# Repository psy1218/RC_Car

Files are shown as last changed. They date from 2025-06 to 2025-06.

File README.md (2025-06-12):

# 🚗 RC Car, R9DS, AT9을 이용한 수동/자동 주행 시스템 구현

> **팀 이름**: 배경근  
> **팀원**: 201901973 배경근, 202201658 박소윤  

---

## 📁 GitHub 디렉토리 구조

### 현재 레포 구조

### 폴더 설명

- **RCcar/**  
  → 최종 통합 버전. 수동/자동/긴급사출/LED 제어가 모두 포함됨.  
  → `cpp/`: 아두이노 제어 코드, `python/`: 라인트레이싱 영상처리 코드

- **auto_mode/**  
  → 자동 주행 실험용. ROI 영역 실험, 필터링 비교 등 테스트 중심

- **manual_mode/**  
  → 수동 조작 실험용. ESC 속도 감쇠 및 PWM LED 점등 테스트

---

### 과거 레포 구조

- **RCcar/**: 수동제어와 LED 제어 코드 
- **auto_detection/**: 영상 기반 라인 인식 초기 실험
- **control/**: 조향 및 속도 제어 실험, PlatformIO 기반

---

---

## 🔔 주의사항 

- 본 프로젝트는 처음에는 기존의 과제 레포에서 진행되었습니다.  
- 하지만 새로운 기능 및 문서화를 위해 별도의 새로운 레포를 생성하였고, 커밋 이력은 초기화되었습니다.  
- 기존 개발 히스토리와 구현 흐름이 궁금한 경우, [**기존 레포지토리 링크(클릭!!)**](https://github.com/psy1218/blink/tree/main/RC_car_project)를 참고해 주세요.

---

## 🎬 실행 영상 - 이미지를 클릭해보세요! 

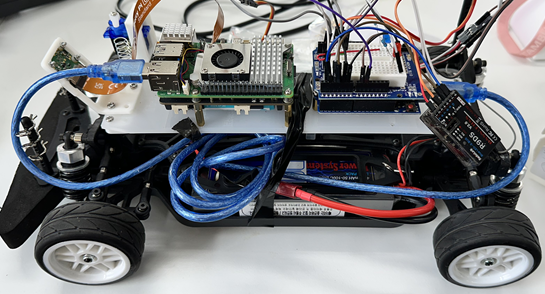
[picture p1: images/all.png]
프로젝트 시연 영상 (https://youtu.be/iogF90Vy1ic)


## 📷 RC카 관련 이미지 
<p align="center">
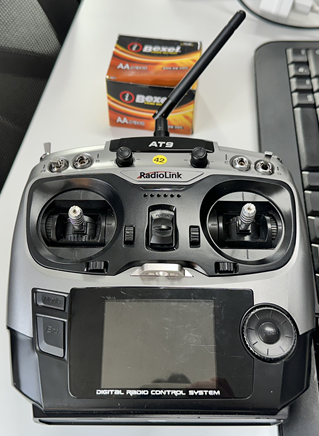
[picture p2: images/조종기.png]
  
  
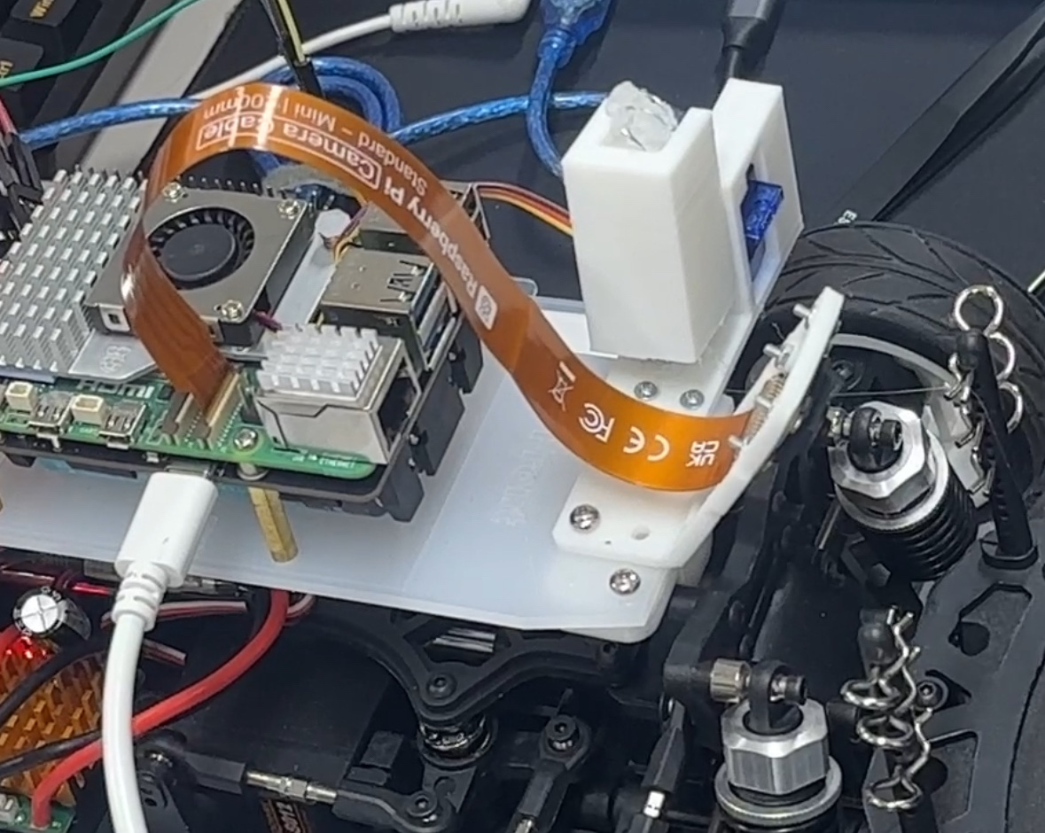
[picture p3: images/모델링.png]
  
</p>

---

## 🎯 RC Car 최종 기능 요약

- **수동 모드 (manual_mode)**  
  → 조종기의 채널 2, 4를 통해 RC카의 속도 및 조향을 직접 제어  
  → PWM 신호를 아두이노에서 감쇠·보정하여 모터로 전달

- **자동 모드 (auto_mode)**  
  → Raspberry Pi + Picamera2를 통해 라인을 인식하고  
  → 계산된 조향값을 시리얼로 아두이노에 전송하여 자동 주행 수행

- **공통 기능**  
  → CH7을 통한 모드 전환, CH6을 통한 긴급 사출 기능  
  → 조향/후진 방향에 따른 LED 시각 피드백  
  → Flask 기반 웹 인터페이스로 실시간 영상 확인

---

## ⚙️ RC카 제어 시스템 구현 방식

### ● 시스템 구조

- Raspberry Pi 5와 Arduino UNO 기반 이중 시스템
- 수동/자동 모드 전환 및 긴급사출 기능 포함
- 시각적 피드백을 위한 LED 장착

---

### ● 모드 전환 (CH7)

- 조종기 CH7의 PWM 신호를 인터럽트로 감지하여 모드 전환  
- `> 1500μs`: 자동 모드  
- `<= 1500μs`: 수동 모드  
- **예시**: 조종기 스위치를 **위로 당기면 자동 모드**, **아래로 내리면 수동 모드**로 전환됨

---

### ● 자동 모드
- **자동 모드 전체 흐름**
  - **아두이노** : 라즈베리파이로부터 조향값(서보모터 각도)을 수신, 수신한 데이터를 바탕으로 각도변경,속도조절,led 제어
      - 지속적으로 시리얼 입력 확인, 개행문자('\n') 단위로 읽어 데이터 수신 및 정수형으로 변환
      - 데이터를 통해 -50(좌측) ~ 50(우측) 서보모터를 회전
      - 급격한 방향전환이 이루어지는 경우( 조향값이  -50 ~ -30 , 30 ~ 50) 속도를 낮춤
      - 방향전환이 있는경우 (조향값이 -50 ~ -43, 7~50) 각 led on/off
  - **라즈베리파이** : 카메라 제어, 로컬서버에서 실시간 화면출력, 라인 위치를 통해 계산된 조향값을 송신
      - picamera2로 카메라 객체를 생성해 라즈베리파이에 연결된 카메라 제어
      - Flask서버를 통해 원격으로 처리화면 송출
      - generate 함수에서 영상 캡쳐 및 라인 디텍션,조향값 계산을 실시하여 지속적으로 시리얼 통신, 비디오 스트리밍  
- **영상 처리**: Picamera2 + OpenCV 사용
- **카메라 설정**:
  - size (640, 480)
  - framerate : 30
  - Brightness : -0.5 (밝기를 어둡게해 equalizeHist 처리를 극명하게 합니다.) 
  - AeEnable: false : (밝기 설정을 위해 자동노출설정을 끕니다.)
- **ROI 설정**:
  - x1영역 (510 ~ 570)
  - x2영역 (190 ~ 250)   
- **전처리 과정**:
  
| 기본 | 카메라 세팅 | 히스토그램 평활화 | 모폴로지 Opening 연산 (30*10) | 
|:---:|:---:|:---:|:---:|
|  스크린샷 2025-06-11 오후 5 14 43|  스크린샷 2025-06-11 오후 4 53 50|  스크린샷 2025-06-11 오후 5 34 42| 스크린샷 2025-06-11 오후 5 36 01 |

| 모폴로지 Opening 연산 (10*30) | 가우시안 블러 | 이진화 |
|:---:|:---:|:---:|
| 스크린샷 2025-06-11 오후 5 36 41 | 스크린샷 2025-06-11 오후 5 39 54 | 스크린샷 2025-06-11 오후 5 40 41  |

  - `equalizeHist`: 히스토그램 평활화  
  - `morphologyEx`: 노이즈 제거  
  - `GaussianBlur`: 블러링  
  - `threshold`: 밝기 기반 이진화
- **라인 인식 및 각도 변환**:  
  
  ---


- **아두이노 제어**:  
  - `90 ± steer_val`로 서보 모터 제어  
  - 조향이 클 경우 저속 회전, 작을 경우 고속 직진  
  - 방향에 따라 LED 점등 (Red: 좌, Blue: 우)

---

### ● 수동 모드

- CH1, CH2의 PWM 입력을 `pulseIn()`으로 수신  
- 속도: 1500μs 기준으로 감쇠 비율(1/5) 적용  
- 조향: `map()`을 사용하여 서보 각도 40~140도로 변환  
- 후진(1450μs 이하) 시 Red/Blue LED 동시 점등  
- 좌/우 회전 시 각 방향에 맞는 LED 점등

---

### ● 긴급 사출 기능 (CH6)

- CH6 신호를 인터럽트로 감지하여  
- `> 1500μs`: 서보를 180도로 회전시켜 구조물 사출  
- `<= 1500μs`: 0도로 복귀

---

### ● 시리얼 통신 (Raspberry Pi ↔ Arduino)

- `/dev/ttyACM*` 포트를 자동 탐색 후 연결
- 라즈베리파이에서 연산된 각도를  33.3333ms(30frame)  마다 9600 buad rate로 아두이노에 전송
- `-50~+50\n` 형태의 문자열로 조향값 전송  
- 연결 예외 발생 시 자동 재시도

---

### ● 영상 스트리밍 (Flask 웹 서버)

- `/video_feed` 경로를 통해 MJPEG 스트리밍 제공  
- 영상 프레임을 JPEG로 압축 후 실시간 전송  
- 자동 주행 상태를 웹에서 시각적으로 확인 가능

---

## 👤 팀원 역할 분담

| 이름 | 역할 |
|---|---|
| 배경근 | 자동 주행 영상 처리 및 각도변환, 시리얼 통신, 웹 스트리밍 |
| 박소윤 | 수동/자동 조작, 핀 구성, LED 제어, 긴급 사출 처리 |

---

## 🧩 핀 연결 표

| 연결 대상 | 수신기 CH | 아두이노 핀 | 설명 |
|---|---|---|---|
| 속도 입력 | CH2 | A0 | PWM 입력 |
| 조향 입력 | CH4 | A1 | PWM 입력 |
| 모드 전환 | CH7 | D2 | PCINT 인터럽트 |
| 긴급 사출 | CH6 | D4 | PCINT 인터럽트 |
| 속도 출력 | - | D9 | ESC 출력 |
| 조향 출력 | - | D6 | 서보모터 제어 |
| 사출 서보 | - | D10 | 구조물 작동 |
| LED 좌회전 | - | D3 | 빨간불 |
| LED 우회전 | - | D5 | 파란불 |
| 공통 전원 | - | 5V | 서보/ESC 전원 |
| 공통 GND | - | GND | 모든 회로 GND |

---

## 🛠 사용 장비 및 도구

- **RC 카**: [링크](http://rclife.co.kr/product/product_detail.asp?product_number=126162)  
- **수신기 (R9DS)**: [링크](https://www.devicemart.co.kr/goods/view?no=15138133)  
- **조종기 (AT9)**: [링크](https://m.xcopter.com/product/radiolink-at9-조종기-r9d-수신기-포함/17946/)  
- **Raspberry Pi 5 + Picamera2 (IMX100)**  
- **Arduino UNO (C++)**  
- **Fusion 360 / Cura**: 사출 장치 모델링 및 3D 출력  
<p align="center">
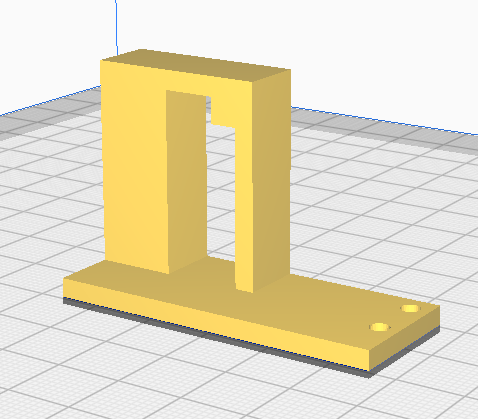
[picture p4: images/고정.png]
  
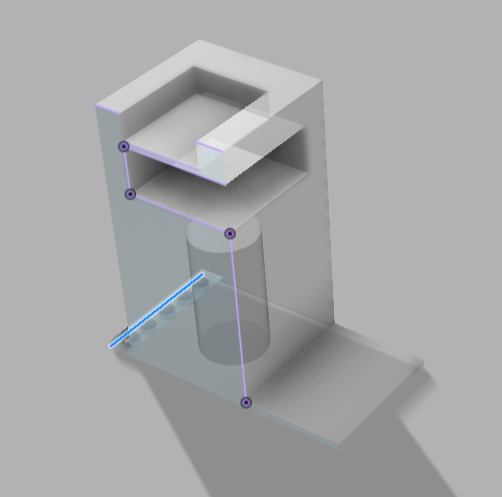
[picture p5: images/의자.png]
  
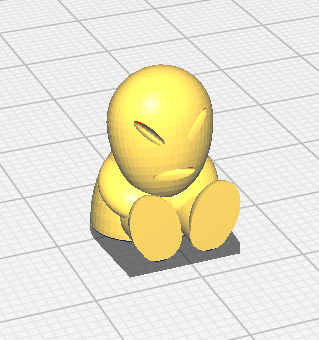
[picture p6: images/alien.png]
  
</p>

---

## 🌟 RC Car 프로젝트의 장점

- **이중 모드**: 수동/자동 모드 전환을 간단한 조종기 조작으로 구현
- **직관적 조작**: 수동 모드에서 조이스틱 조작만으로 직관적 주행 가능
- **AI 라인 추종**: 자동 모드에서 실시간 영상 처리 기반으로 정밀한 라인 추적
- **비주얼 피드백**: 웹 인터페이스를 통한 현재 상황 실시간 확인 가능
- **상태별 LED 피드백**: 주행 방향에 따라 LED 피드백으로 안전성 강화
- **긴급 사출**: 긴급 상황 대비한 **3D 프린팅 기반 물리적 구조물 구현**
- **일관성 유지**: 시리얼 통신 기반의 **라즈베리파이-아두이노 연동**으로 하드웨어 제어 일관성 유지

---

## 👣 프로젝트 히스토리

### 1단계: 수동 주행 & 영상 스트리밍 시작

- Raspberry Pi → Flask 웹서버로 카메라 영상 확인
- Arduino → 수신기/조종기/RC카 PWM 연결로 수동 주행 구현

### 2단계: 자동 주행 프로토타입 개발

- Python: Picamera2 기반 ROI 설정, PID 사용해서 line detection 
- C++: 시리얼 조향값 수신 → 속도 고정 주행

### 3단계: 기능 확장

- C++: 수동 모드 조향 PWM 제어 추가
- C++: 모든 모드에 LED 제어 구현
- Python: 영상 하단 및 상단 분할, 가중치 기반 steering 연산

### 4단계: 인터럽트 기능 추가 & 필터 최적화

- C++: PCINT로 모드 전환/긴급 사출 처리
- Python: 그림자/빛 처리 강화  
  (Picamera2 세팅, 전처리 파라미터 조정, 컨투어 필터링 강화)

### 5단계: 모든 기능 통합 및 시연

- 모든 모드 및 기능 통합 완료
- 안정성 개선 및 테스트 완료

---

## ⚠ 프로젝트 시행착오 & 배운 점

1. **PWM 함수 오용 → ESC 3대 고장**

    PWM 제어 시 `analogWrite()`를 잘못 사용하여 RC카 ESC가 총 3대 고장남.  
    `analogWrite()`는 서보/ESC용이 아닌 일반 PWM용 함수로, RC 제어에는 `writeMicroseconds()` 사용이 필수임을 깨달음.

2. **조종기 배터리 장착 실수 → 폭발 사고 발생**

    조종기 건전지 8개 중 1개를 반대로 끼워 배터리가 터지는 사고 발생.  
    전원 연결 전 극성 확인의 중요성을 직접 체감함.

3. **조종기 ↔ RC카 전원 순서 오류 → 주행 방향 반전**

    조종기와 RC카의 전원 ON 순서에 따라 주행 방향이 반대로 설정되는 현상 발생.  
    정확한 시퀀스에 따른 장비 초기화의 중요성을 학습함.

4. **밝기/그림자 영향으로 라인 인식 불량 → 영상 처리 개선**

    자동 주행 시 밝기 변화와 그림자에 따라 라인을 탐지하지 못하는 문제 발생.  
    이를 해결하기 위해 카메라 설정(노출, 밝기 등)을 조정하고,  
    `equalizeHist`, `morphologyEx`, `GaussianBlur`, `threshold`,  
    컨투어 필터링 등 다양한 전처리 기법을 적용하여 극복함.
<p align="center">
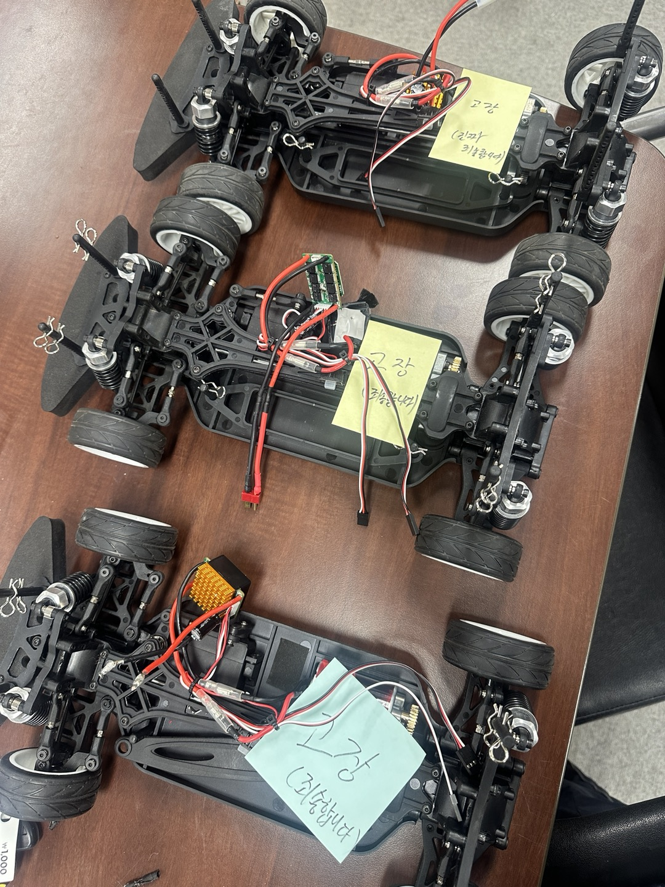
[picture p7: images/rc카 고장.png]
  
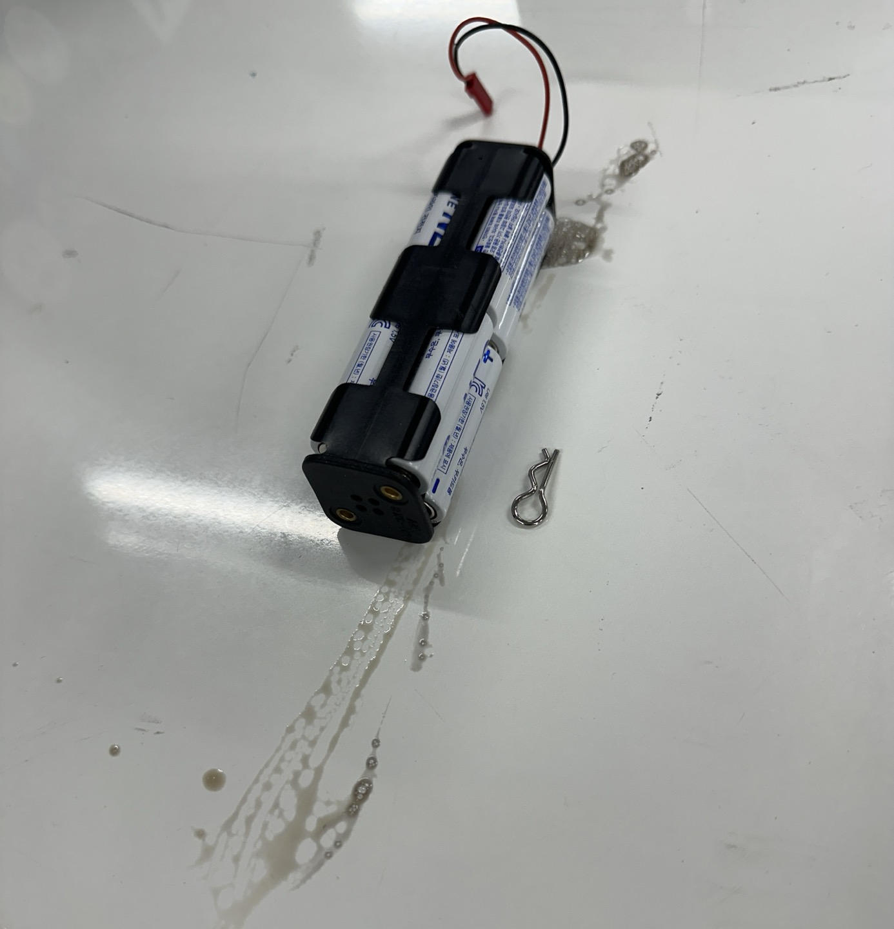
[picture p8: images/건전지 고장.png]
  
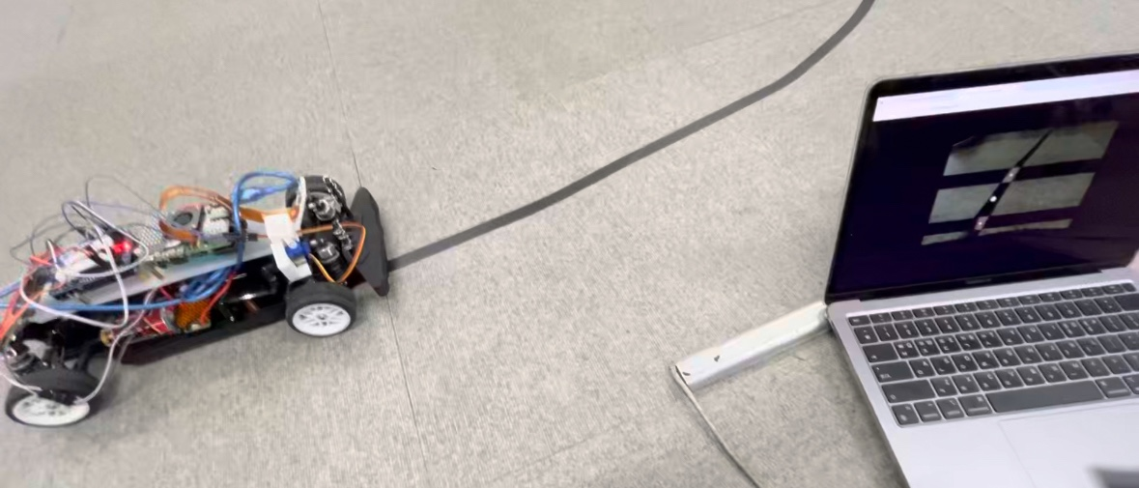
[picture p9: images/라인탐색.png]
  

</p>

---

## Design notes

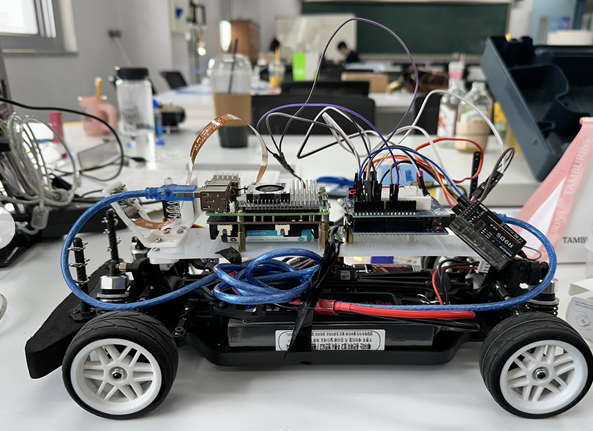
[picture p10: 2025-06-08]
images/전체샷.png

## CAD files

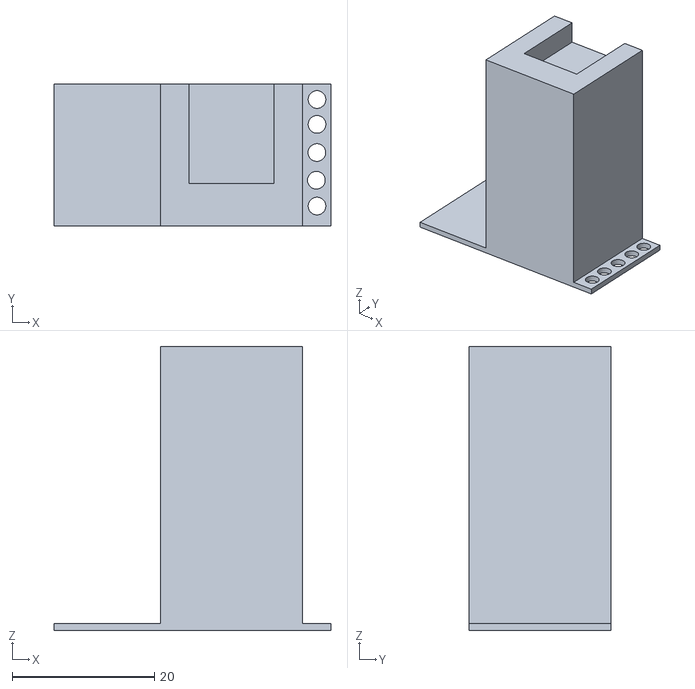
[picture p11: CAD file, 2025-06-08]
3D_printer/chair.stl
39.0 x 20.0 x 40.0

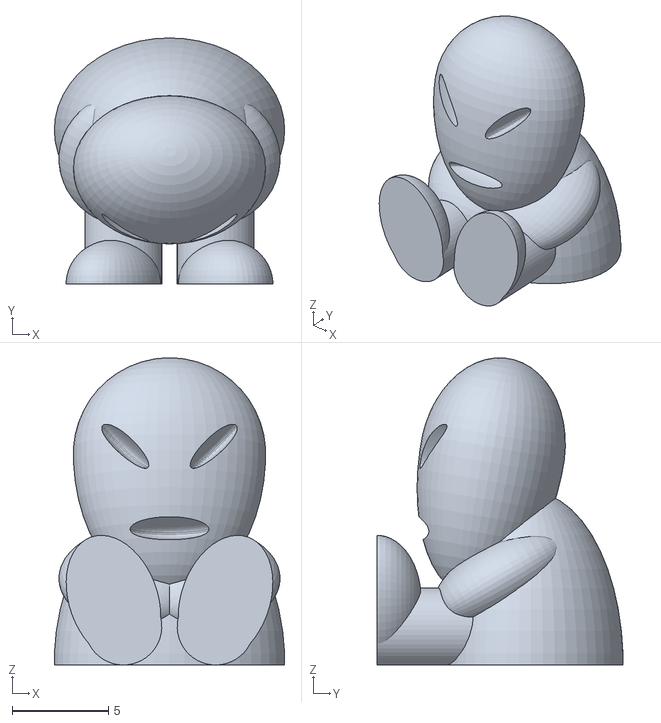
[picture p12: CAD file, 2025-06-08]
3D_printer/alien_pilot_tiny.stl
12.0 x 12.8 x 16.0

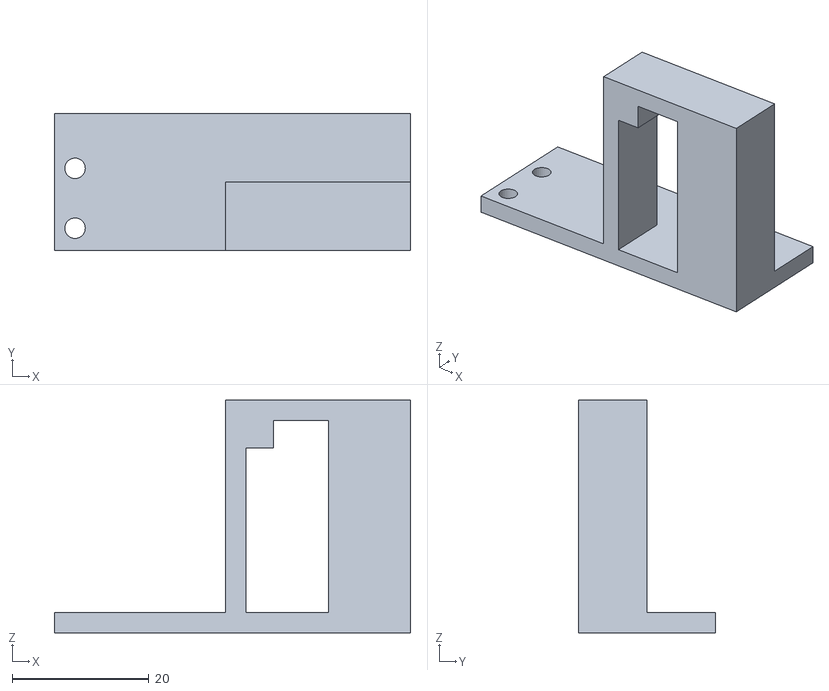
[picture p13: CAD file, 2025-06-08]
3D_printer/emergency ejection.stl
52.0 x 20.0 x 34.0

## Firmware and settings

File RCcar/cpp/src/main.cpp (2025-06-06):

#include <Arduino.h> //아두이노 기본 라이브러리
#include <Servo.h> //rc car의 속도와 조향을 제어하기 위한 서보 라이브러리
#include <PinChangeInterrupt.h> //인터럽트를 실시간으로 처리하기 위한 라이브러리

// === 핀 정의 ===
#define THROTTLE_IN A0      // 수신기에서 속도 PWM 입력
#define STEER_IN A1     // 수신기에서 조향 PWM 입력
#define THROTTLE_OUT 9   // ESC pwm 출력 핀
#define STEER_OUT 6     // 서보 pwm 출력 핀
#define LED_RED 3    //led red 핀
#define LED_blue 5   //led blue 핀
#define CH7_PIN 2        // 모드 전환용 PWM 핀
#define CH6_PIN 4        // 긴급사출 작동용 PWM 핀
#define AUX_SERVO_PIN 10 // 긴급사출 서보모터 핀

// 상태 저장 변수
bool isBackward = false;  // 후진 상태 여부
bool isTurningLeft = false; // 좌회전 상태 여부
bool isTurningRight = false; // 우회전 상태 여부

// === 객체 및 변수 ===
Servo esc; // ESC 제어용 서보
Servo steer_servo; // 조향 제어용 서보
Servo aux_servo; // 긴급사출 제어용 서보

// CH7 관련 - 모드 전환용: 수동/자동
volatile unsigned long ch7_start = 0; // CH7 PWM 측정용
volatile uint16_t ch7_pulse = 1500; // CH7 PWM 값 (중립 1500us)
volatile bool new_ch7 = false; // CH7 값이 갱신되었는지 여부
bool mode = false; // false: 수동, true: 자동

// CH6 관련 - 긴급사출용용
volatile unsigned long ch6_start = 0; // CH6 PWM 측정용
volatile uint16_t ch6_pulse = 1500; // CH6 PWM 값 (중립 1500us)
volatile bool new_ch6 = false; // CH6 값이 갱신되었는지 여부

// 시리얼 수신 처리용
String inputString = ""; // 시리얼 입력 문자열
bool stringComplete = false; // 문자열 수신 완료 여부

void ch7_ISR(); // CH7 PWM 측정 인터럽트 선언
void ch6_ISR(); // CH6 PWM 측정 인터럽트 선언

void setup(){
    Serial.begin(9600); // 시리얼 통신 초기화
    esc.attach(THROTTLE_OUT); // ESC는 핀 9번에 연결
    steer_servo.attach(STEER_OUT);  // 조향 서보는 핀 6번에 연결
    aux_servo.attach(AUX_SERVO_PIN); // 긴급사출 서보는 핀 10번에 연결

    pinMode(LED_RED, OUTPUT); // LED 빨간색 핀 출력 설정
    pinMode(LED_blue, OUTPUT); // LED 파란색 핀 출력 설정
    pinMode(CH7_PIN, INPUT_PULLUP); // CH7 모드 전환용 핀 입력 설정 (풀업 저항 사용)
    pinMode(CH6_PIN, INPUT_PULLUP); // CH6 긴급사출용 핀 입력 설정 (풀업 저항 사용)

    // === 초기화 ===  setting 단계에서 LED를 꺼져있도록 설정
    digitalWrite(LED_RED, LOW); // LED 빨간색 초기화
    digitalWrite(LED_blue, LOW); // LED 파란색 초기화

    esc.writeMicroseconds(1500); // ESC 초기값 중립
    steer_servo.write(90); // 서보 초기값 중립 (90도)
    aux_servo.write(0); // 긴급사출 서보 초기값 -> OFF 상태
    delay(2000); // 초기화 대기 시간

    //CHANGE 이용으로 falling, rising 전부 감지하여 pwm 측정
    attachPCINT(digitalPinToPCINT(CH7_PIN), ch7_ISR, CHANGE); // CH7 모드 전환용 PWM 측정 인터럽트 설정 
    attachPCINT(digitalPinToPCINT(CH6_PIN), ch6_ISR, CHANGE); // CH6 긴급사출용 PWM 측정 인터럽트 설정

    // === 시리얼 입력 초기화 ===
    inputString.reserve(20);
}

void loop(){
    // === CH7 모드 갱신 ===
    if (new_ch7){ //PCINT 인터럽트로 CH7 값이 갱신되었을 때
        new_ch7 = false; // 갱신된 상태를 false로 설정 - 다음 갱신을 위해
        mode = (ch7_pulse > 1500); // true: 자동모드(auto_mode), false: 수동모드(manual_mode)
    }

    // === CH6 서보 제어 ===
    if (new_ch6){ //PCINT 인터럽트로 CH6 값이 갱신되었을 때
        new_ch6 = false; // 다음 갱신을 위해 false로 설정
        if (ch6_pulse > 1500) {// CH6 핀의 펄스가 1500us보다 크면 긴급사출 서보를 ON 상태로 설정
            aux_servo.write(180); // ON 상태
        }
        else{
            aux_servo.write(0); // OFF 상태
        }
    }

    // === 자동 모드 === auto_mode
    if (mode){
        while (Serial.available()){ // 시리얼 입력이 있는 동안 - 라즈베리파이5에서 입력된 steer 값이 있는 동안
            // 시리얼 입력을 읽어 문자열로 저장
            char inChar = (char)Serial.read(); // 시리얼로부터 문자 단위로 읽기
            if (inChar == '\n') // 줄바꿈 문자가 들어오면
                stringComplete = true; // 문자열 수신 완료로 설정
            else
                inputString += inChar; // 입력된 문자를 문자열에 추가
        }
        //시리얼 입력값을 받고, 문자열과 줄바꿈 문자에 대한 처리 


        if (stringComplete) { // 문자열 수신이 완료되었을 때 = 줄바꿈 문자가 들어와서 한 문자열을 다 읽었을 때
            int steer_val = inputString.toInt(); // 문자열을 정수로 변환: 입력된 steer 값은 문자열이기 때문에 정수형으로 변환 시켜줘야함.
            steer_val = constrain(steer_val, -50, 50); // steer 값의 범위를 -50에서 50으로 제한
            // 범위를 제한하는 이유는, 라즈베리파이5에서 입력된 steer 값이 -50에서 50 사이로 제한되어 있기 때문이다.
            // 또한 이 범위를 벗어나는 값은 조향에 영향을 주지 않도록 하기 위함이다.
            int servo_pos = constrain(90 + steer_val, 40, 140); // 서보 위치 계산: 중립 90도에서 steer 값만큼 이동
            //최저, 최대 조향 값을 설정하지 않은 이유는 갑작스러운 조향을 방지하기 위함이다.
            steer_servo.write(servo_pos); // 계산된 steer 값을 서보에 작용하여 조향 제어가 가능하게 한다.

            if (servo_pos < 90 - 30 || servo_pos > 90 + 30){ // 조향이 좌우로 30도 이상 벗어났을 때
                // 조향이 좌회전, 우회전 상태일 때
                esc.writeMicroseconds(1553); // 평소 속도보다 약간 낮은 속도로 회전하여 안정적으로 회전할 수 있도록 하였다.
            }
            else{
                esc.writeMicroseconds(1555); // 조향이 중립 상태일 때 상대적으로 높은 속도로 직진할 수 있도록 하였다.
            }

            // 다음 문자열을 받기 위해 밑의 작업을 수행한다.
            inputString = ""; // 문자열 초기화
            stringComplete = false; // 문자열 수신 완료 상태 초기화

            // 조향과 후진에 따른 led 제어를 위한 작업
            int angle = servo_pos; // 서보 위치를 angle 변수에 저장

            if (angle > 93){ // 조향이 좌회전 상태일 때
                isTurningLeft = true; // 좌회전 상태로 설정
                isTurningRight = false; // 우회전 상태는 false로 설정
            }
            else if (angle < 83){ // 조향이 우회전 상태일 때
                isTurningRight = true; // 우회전 상태로 설정
                isTurningLeft = false; // 좌회전 상태는 false로 설정
            }
            else { // 조향이 중립 상태일 때
                isTurningLeft = false;
                isTurningRight = false;
            }

            // === LED 출력 (자동 모드 회전 방향 기준)
            if (isTurningLeft){  // 좌회전 상태일 때
                // LED 빨간색 켜고, 파란색 끔
                digitalWrite(LED_RED, 1);
                digitalWrite(LED_blue, 0);
            }
            else if (isTurningRight){ // 우회전 상태일 때
                // LED 빨간색 끄고, 파란색 켬
                digitalWrite(LED_RED, 0);
                digitalWrite(LED_blue, 1);
            }
            else { // 조향이 중립 상태일 때
                digitalWrite(LED_RED, 0);
                digitalWrite(LED_blue, 0);
            }
        }
    }
    else{ // === 수동 모드 === manual_mode
        // pulseIn 함수는 지정된 핀에서 HIGH 상태가 지속되는 시간을 마이크로초 단위로 반환
        // 25000us(25ms) 이상의 신호가 없으면 타임아웃으로 간주하여 0을 반환
        int pwm_throttle = pulseIn(THROTTLE_IN, HIGH, 25000); //pulseIn 함수를 사용하여 THROTTLE_IN 핀에서 PWM 신호를 읽어옴
        int pwm_steer = pulseIn(STEER_IN, HIGH, 25000); // pulseIn 함수를 사용하여 STEER_IN 핀에서 PWM 신호를 읽어옴

        int neutral = 1500; // 중립값 설정 (1500us)
        int reduced_pwm; // 속도를 줄이기 위한 변수


        // pwm 값을 제어하여 속도를 줄이는 이유는, 
        // 높은 pwm 값이 들어오면 차량이 급격하게 움직일 수 있기 때문에
        // 차량의 안전성을 위해 속도를 줄이는 것이다.
        if (pwm_throttle > neutral){ // 수신기에서 받은 속도 값이 중립값보다 크면
            reduced_pwm = neutral + (pwm_throttle - neutral) / 5; // 중립값에 비례하여 속도를 줄임
        }
        else if (pwm_throttle < neutral){ // 수신기에서 받은 속도 값이 중립값보다 작으면
        reduced_pwm = neutral - (neutral - pwm_throttle) / 5; // 중립값에 비례하여 속도를 줄임
        }
        else{
        reduced_pwm = neutral;  // 수신기에서 받은 속도 값이 중립값과 같으면 속도를 0으로 설정
        }

        // 수신기에서 받은 pwm 속도 값을 연산한 후 계산된 값을 esc에 전달
        esc.writeMicroseconds(reduced_pwm);


        // === 조향 제어 ===
        int angle = map(pwm_steer, 1000, 2000, 40, 140); // 수신기에서 받은 조향 PWM 값을 40도에서 140도로 매핑
        angle = constrain(angle, 40, 140); // 조향 각도를 40도에서 140도로 제한
        //constrain 함수는 주어진 값이 지정된 범위 내에 있도록 제한하는 함수
        steer_servo.write(angle); // 계산된 조향 각도를 서보에 전달하여 조향 제어

        // === LED 제어 ===
        // === isBackward 판별만 따로 처리 ===
        if (reduced_pwm < 1450){ // 수신기에서 받은 속도 값이 중립값보다 작으면 후진 상태로 판단
            // 후진 상태일 때는 LED를 켜고, 조향 방향에 관계 없이 후진 상태로 판단
            isBackward = true;
        }
        else if (reduced_pwm >= 1450){
            isBackward = false; // 수신기에서 받은 속도 값이 중립값보다 크거나 같으면 후진 상태가 아님
        }

        // === angle에 따라 회전 방향 판단 (정지 여부와 관계 없이) ===
        if (angle > 93){ // 조향 각도가 93도보다 크면 좌회전 상태로 판단
            isTurningLeft = true; // 좌회전 상태로 설정
            isTurningRight = false; // 우회전 상태는 false로 설정
        }
        else if (angle < 80){ // 조향 각도가 80도보다 작으면 우회전 상태로 판단
            isTurningRight = true; // 우회전 상태로 설정
            isTurningLeft = false; // 좌회전 상태는 false로 설정
        }
        else{ // 조향 각도가 80도와 93도 사이에 있으면 정지 상태로 판단
            isTurningLeft = false; 
            isTurningRight = false;
        }

        // === LED 출력 (정지 + 회전 방향 반영)
        if (isBackward) {   // 후진 상태일 때
            // LED 빨간색과 파란색을 켬
            digitalWrite(LED_RED, 1);
            digitalWrite(LED_blue, 1);
        }
        else if (isTurningLeft)   { // 좌회전 상태일 때
            // LED 빨간색 켜고, 파란색 끔
            digitalWrite(LED_RED, 1);
            digitalWrite(LED_blue, 0);
        }
        else if (isTurningRight){ // 우회전 상태일 때
            // LED 빨간색 끄고, 파란색 켬
            digitalWrite(LED_RED, 0);
            digitalWrite(LED_blue, 1);
        }
        else{ // 조향이 중립 상태일 때
            // LED 빨간색과 파란색을 끔
            digitalWrite(LED_RED, 0);
            digitalWrite(LED_blue, 0);
        }
    }
} //

// === CH7 PWM 측정 인터럽트 ===
void ch7_ISR(){
    if (digitalRead(CH7_PIN) == HIGH) // CH7 핀의 상태가 HIGH일 때
        ch7_start = micros(); // 시작 시간을 기록
    else if (ch7_start)    { // CH7 핀의 상태가 LOW로 바뀌었고, 시작 시간이 기록되어 있다면
        // CH7 핀의 상태가 LOW로 바뀌었을 때, 시작 시간과 현재 시간을 비교하여 펄스 길이를 계산
        ch7_pulse = micros() - ch7_start; // 펄스 길이 계산
        new_ch7 = true; // 새로운 CH7 값이 갱신되었음을 표시
        ch7_start = 0; // 시작 시간 초기화
    }
}

// 위의 CH7_ISR 함수와 동일한 구조로 CH6_ISR 함수가 이루어져있음.
// === CH6 PWM 측정 인터럽트 ===
void ch6_ISR(){
    if (digitalRead(CH6_PIN) == HIGH) 
        ch6_start = micros();
    else if (ch6_start){
        ch6_pulse = micros() - ch6_start;
        new_ch6 = true;
        ch6_start = 0;
    }
}

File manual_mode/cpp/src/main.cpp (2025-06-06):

#include <Arduino.h>
#include <Servo.h>

// === 핀 정의 ===
#define THROTTLE_IN A0 // 수신기에서 속도 PWM 입력
#define STEER_IN A1    // 수신기에서 조향 PWM 입력
#define THROTTLE_OUT 9 // ESC 출력
#define STEER_OUT 6    // 서보 출력

#define LED_RED 3 // LED 빨간색 핀
#define LED_GREEN 5 // LED 녹색 핀

Servo esc; // ESC 제어용 서보
Servo steer_servo; // 조향 제어용 서보

void setup()
{
    esc.attach(THROTTLE_OUT);
    steer_servo.attach(STEER_OUT);

    pinMode(LED_RED, OUTPUT);
    pinMode(LED_GREEN, OUTPUT);

    esc.writeMicroseconds(1500); // ESC 중립
    steer_servo.write(90);       // 서보 중립 (90도)
    delay(2000);
}

void loop()
{
    // === 속도 제어 ===
    int pwm_throttle = pulseIn(THROTTLE_IN, HIGH, 25000);
    int neutral = 1500;
    int reduced_pwm;

    if (pwm_throttle > neutral)
    {
        reduced_pwm = neutral + (pwm_throttle - neutral) / 5;
    }
    else if (pwm_throttle < neutral)
    {
        reduced_pwm = neutral - (neutral - pwm_throttle) / 5;
    }
    else
    {
        reduced_pwm = neutral;
    }
    esc.writeMicroseconds(reduced_pwm);

    // === 조향 제어 ===
    int pwm_steer = pulseIn(STEER_IN, HIGH, 25000);  // 예: 1000~2000us
    int angle = map(pwm_steer, 1000, 2000, 40, 140); // 중립 90도
    angle = constrain(angle, 40, 140);
    steer_servo.write(angle);

    // === LED 제어: 후진 기준 ===
    if (pwm_throttle < 1450)
    {
        //int reverse_intensity = map(1500 - pwm_throttle, 0, 500, 0, 255); // 후진 속도 비례
        //analogWrite(LED_RED, reverse_intensity);
        //analogWrite(LED_GREEN, reverse_intensity);
        analogWrite(LED_RED, 1);
        analogWrite(LED_GREEN, 1);
    }
    else
    {
        // === LED 제어: 조향 기준 ===
        if (angle < 87)
        {
            // int brightness = map(90 - angle, 0, 50, 0, 255); // 좌회전 세기 → 밝기
            //  analogWrite(LED_RED, brightness);
            analogWrite(LED_RED, 1);
            analogWrite(LED_GREEN, 0);
        }
        else if (angle > 92)
        {
            //  int brightness = map(angle - 90, 0, 50, 0, 255); // 우회전 세기 → 밝기
            //   analogWrite(LED_GREEN, brightness);
            analogWrite(LED_GREEN, 1);
            analogWrite(LED_RED, 0);
        }
        else
        {
            analogWrite(LED_RED, 0);
            analogWrite(LED_GREEN, 0);
        }   
    }
}

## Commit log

2025-06-05 commit 하고 첫 정리 (과거의 레포에서 작업한 것을 새로운 레포에서 작업하느냐고 커밋 기록이.. 초기화... 대신 과거의 레포 링크 올려두기!!!)
2025-06-05 최종 rc car 코드 커밋
2025-06-06 최종 cpp, python 코드 주석 추가, 과거의 수동, 자동 모드 코드 추가 (과거 기록 저장장)
2025-06-06 git readme 작성 중 . . . . . . . .
2025-06-08 readme 작성. .. 중 . .
    [alien_pilot_tiny.stl, chair.stl, emergency ejection.stl]
